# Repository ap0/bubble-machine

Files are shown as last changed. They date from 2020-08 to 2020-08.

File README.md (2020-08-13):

# Bubble Machine

This is the design and code for my bubble machine.  You can find more info at the blog post here: https://medium.com/@adamargo/an-arduino-powered-3d-printed-bubble-machine-4cf9241d1459

## Notes

The parts were designed from scratch in Fusion 360.  The electronics were designed to use a 5V input supply so they could be powered by phone batteries.  At max settings, my power supply reported that it was consuming about 1.4A, so I'd be safe and round up to 2A for the output on the USB port.

The Arduino code runs the stepper motion in the event loop so minimize jitters when updating the LCD.  The I2C LCD is very slow to update.  A better version might figure out how to output directly without I2C.

## Parts List

To build this, you will need:

* at least 4 feet of 3/8" dowel rods ($1 at Home Depot)
* 4x M3x10mm screws and square nuts (I bought these nuts: https://www.amazon.com/Honbay-100pcs-Stainless-Steel-Square/dp/B06XPFLNBS -- they are a little thicker than the nuts that come on e.g. the Prusa).  These can be longer than 10mm if you don't have any; that's just the minimum.
* 4x M2.5x12mm M2 screws and nuts for the LCD -- these can be a little longer if you don't have 12mm -- up to 15mm should be fine, they'll just stick out inside the housing.
* Type 130 12V motor (I used the ones from this kit https://www.amazon.com/EUDAX-Electric-Magnetic-Connector-Propeller/dp/B07GDP2FCL -- the red housing seems to be the key, because they're a standard type 130 size motor, but lower voltage ones do not work and will burn up)
* Arduino Nano
  * I got one with pins soldered onto the board. This makes it easy to slot into the protoboard.
* 2 10k+Ω potentiometers (ones with a 7mm shaft diameter)
* A 16x2 I2C LCD module (I got these: https://www.amazon.com/GeeekPi-Character-Backlight-Raspberry-Electrical/dp/B07S7PJYM6) -- this part isn't required for the machine to function -- you could easily redesign the housing to not use it.
* 50x75mm protoboard
* 2x 2-pin terminal blocks
* ULN2003A Darlington array and socket
* IRF520 or RFP30N06LE MOSFET (it has to be a logic-level MOSFET, i.e. can be driven by 5V from Arduino)
* 2.54mm header pins and sockets
* 4 .1 μF capacitors
* 2 diodes
* A 5V 2.0A power supply (1.4A is the highest output I've seen on the meter -- the fan motor draws a lot of energy at high speeds) -- if you limited the MOSFET's output then you could probably live with 1A.  I'm using an Anker battery pack and it works fine.

## 3D printed parts

Total print time is around 24 hours at .15mm quality settings in PrusaSlicer for a MK3S.  You can't quite fit everything onto the bed at once.  The parts are designed to have a face to print on and should require minimal supports.  You will have to block the gap on the outer ring of the fan mount.

### Supports you should add

I tried to make it use minimal supports.  You should only need them on three of the parts:
* On the blower fan motor holder, you should add a support under the small area that's a clearance for the cover to sit flush, and potentially to hold up the other side of the neck.  I added a small slab in PrusaSlicer and it worked fine.
* On the two knobs you'll have to add supports to the bottom because it's got some inset holes to sit flush over the potentiometer nuts.

I printed mine in a few different filaments.  I used orange Prusament PETG, the gray Prusa (not Prusament) PLA that came with the MK3s, and yellow and blue Hatchbox PLA.  No real rhyme or reason to it other than aesthetics.  PLA works well for the housing as it's quite large.  The housing uses about 100g of filament and took about 11 hours to print.  I really like Hatchbox PLA -- the colors are very nice, it's not very expensive, and it prints great.  I also printed the knobs in the same color of the part they control, just as a nice touch.

The bubble wand hub is the most challenging part to print.  I found that using 0.2mm layer heights worked slightly better to deposit a little more filament on the first layer to get the ridges to stick.  My final print of it had only two of those instances not stick.  The quality and calibration of your printer will make or break this part.

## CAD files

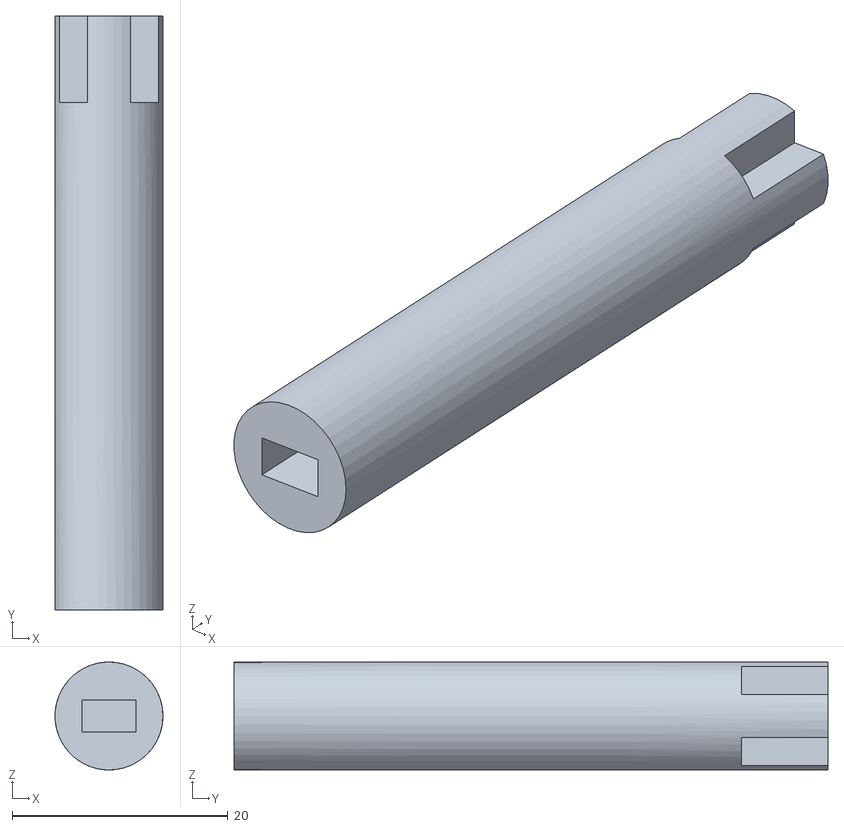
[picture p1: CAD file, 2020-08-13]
stl/BubbleMachine v25_BubbleMachine v25_Spindle_2_Spindle_Spindle.stl
10.0 x 55.0 x 9.99

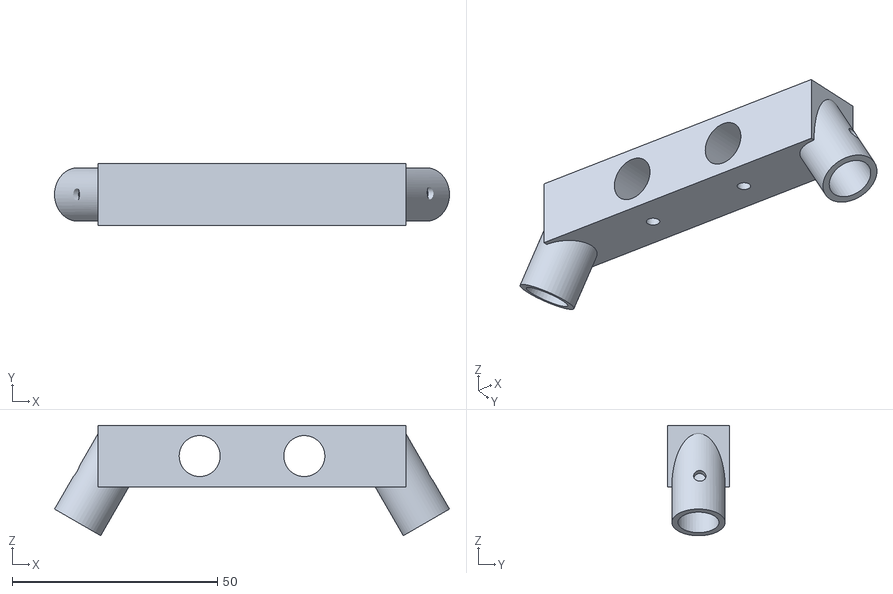
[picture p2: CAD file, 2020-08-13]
stl/BubbleMachine v25_BubbleMachine v25_Leg Mount _1_Leg Mount_.stl
96.3 x 15.0 x 26.9

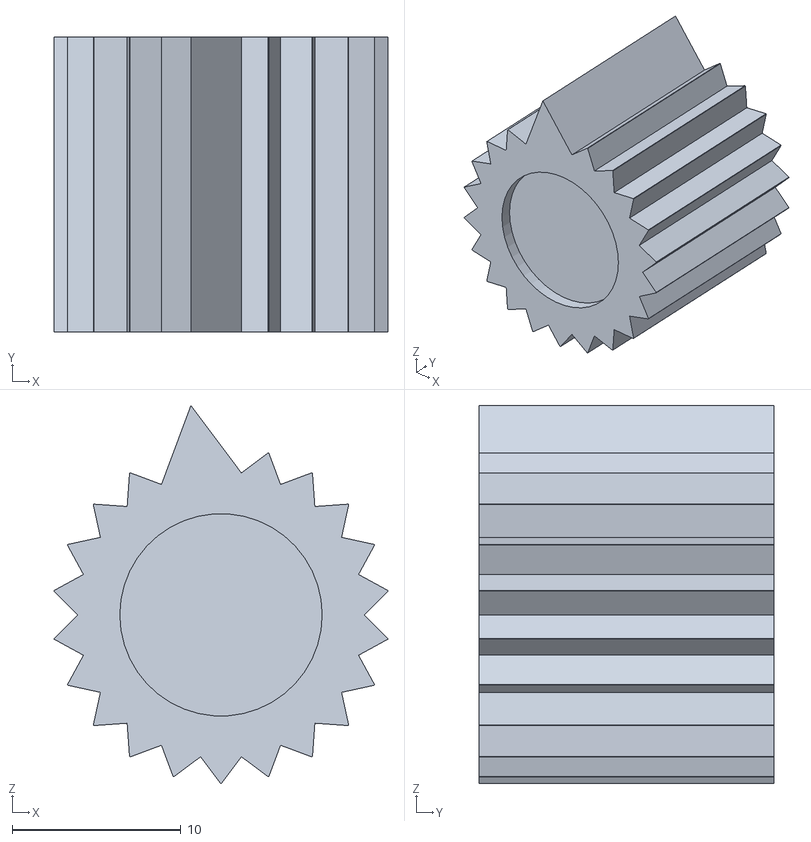
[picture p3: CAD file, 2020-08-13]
stl/BubbleMachine v25_BubbleMachine v25_Electronics Housing_1_KnurledKnob_1_Knob_KnurledKnob.stl
19.8 x 17.5 x 22.4

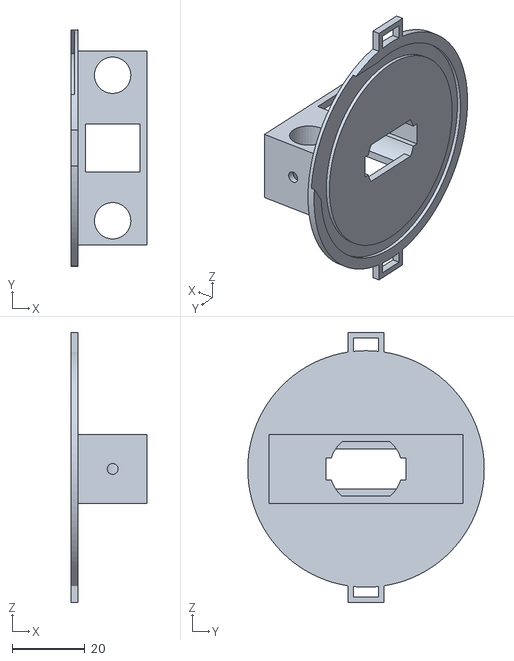
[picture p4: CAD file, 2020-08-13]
stl/BubbleMachine v25_BubbleMachine v25_Blower_1_Motor Holder_1_Holder_Motor Holder.stl
21.0 x 65.0 x 74.2

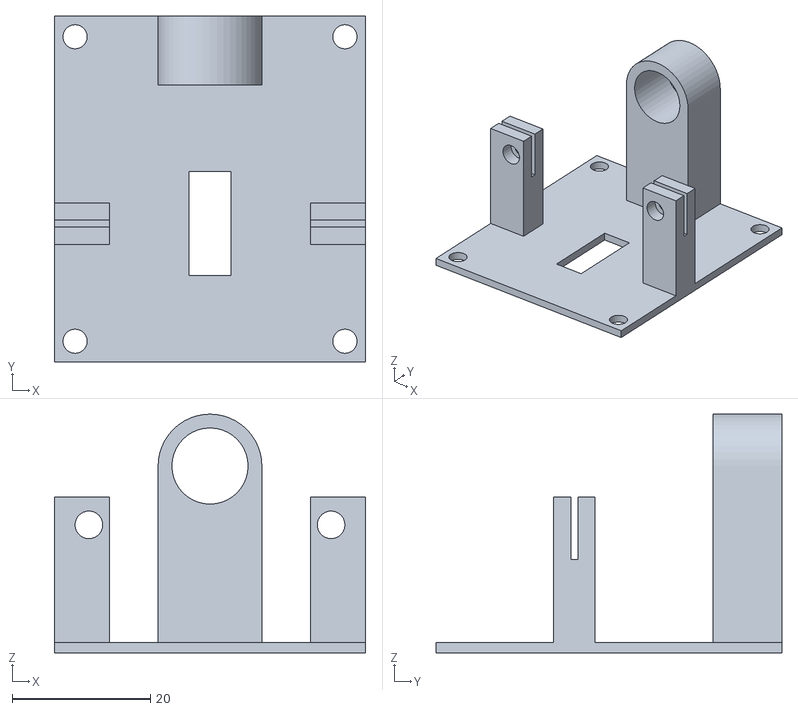
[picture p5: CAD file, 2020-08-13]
stl/BubbleMachine v25_BubbleMachine v25_Wand Motor Base_2_Base_Wand Motor Base.stl
45.0 x 50.0 x 34.5

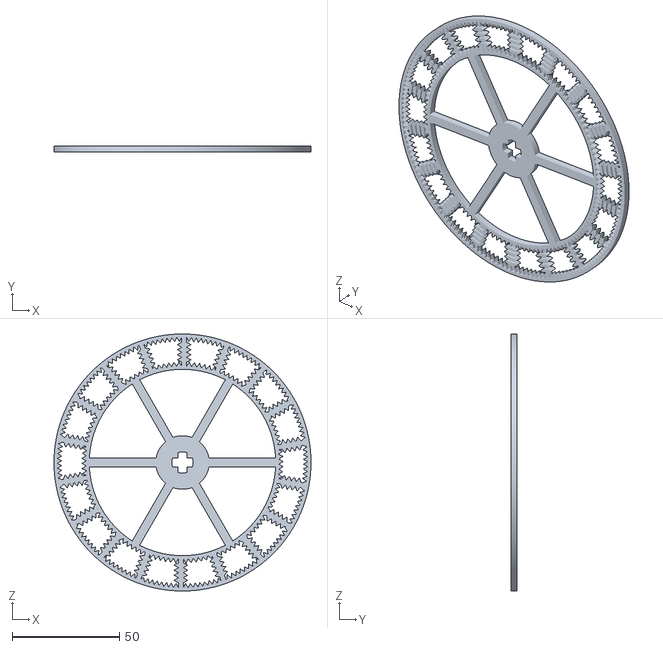
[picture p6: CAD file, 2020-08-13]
stl/BubbleMachine v25_BubbleMachine v25_Wand Wheel_1_Wheel_Wand Wheel.stl
120.0 x 3.00 x 120.0

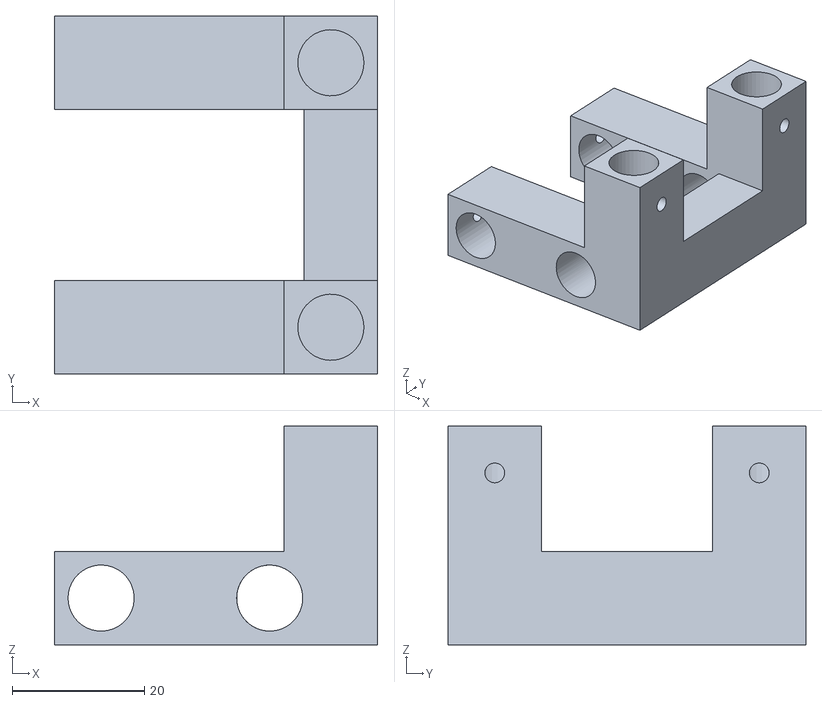
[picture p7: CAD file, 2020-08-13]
stl/BubbleMachine v25_BubbleMachine v25_Blower Frame Mount_1_Blower Frame Mount_.stl
48.9 x 54.1 x 33.1

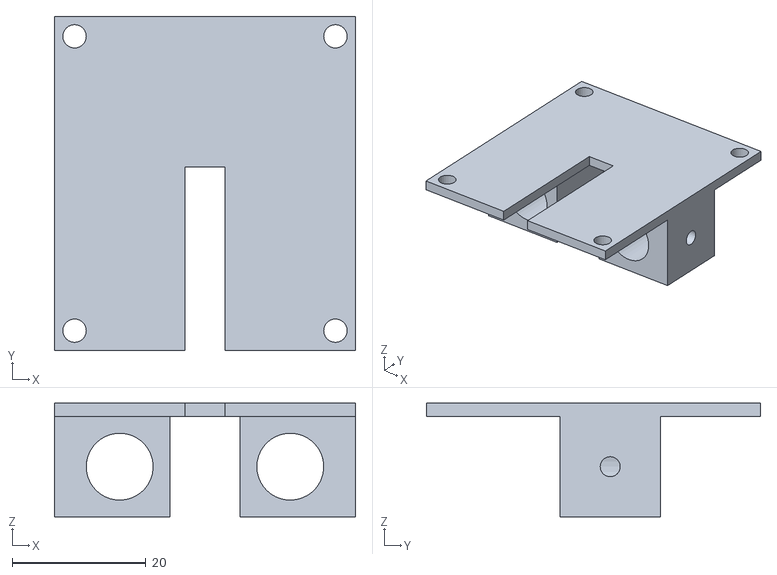
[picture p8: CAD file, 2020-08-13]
stl/BubbleMachine v25_BubbleMachine v25_Wand Motor Stand Base_1_Motor Stand Base_.stl
45.0 x 50.0 x 17.0

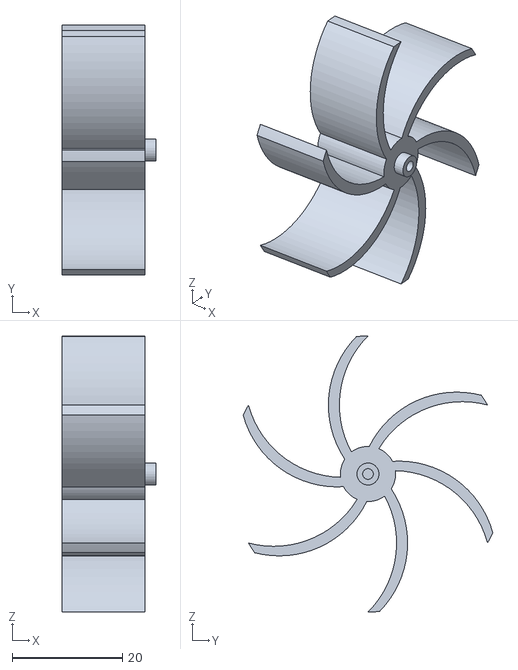
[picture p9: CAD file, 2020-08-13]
stl/BubbleMachine v25_BubbleMachine v25_Blower_1_Impeller_1_Impeller_Impeller.stl
17.0 x 45.2 x 50.0

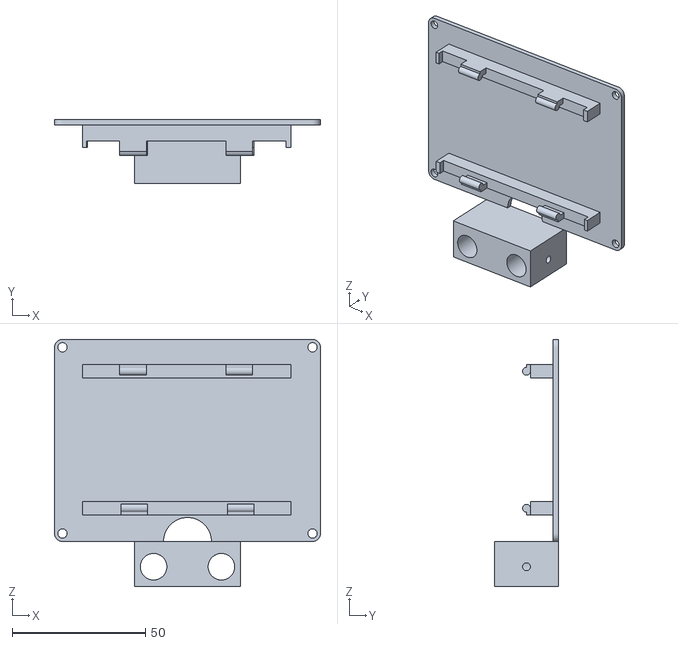
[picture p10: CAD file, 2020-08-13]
stl/BubbleMachine v25_BubbleMachine v25_Electronics Housing_1_Housing_1_Back_1_Back_Back.stl
100.0 x 24.0 x 93.0

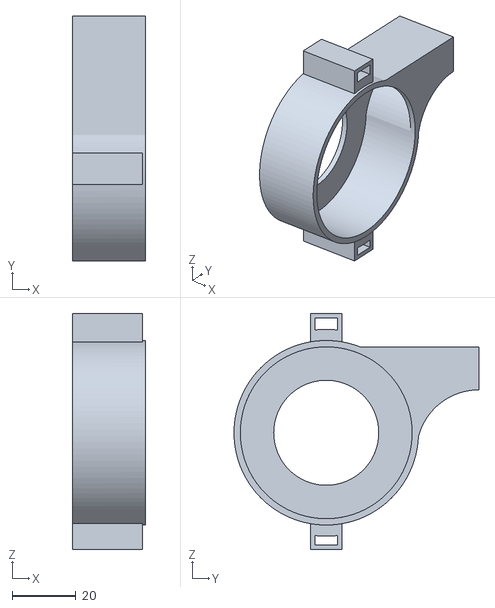
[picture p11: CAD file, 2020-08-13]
stl/BubbleMachine v25_BubbleMachine v25_Blower_1_Blower Cover_1_Cover_Blower Cover.stl
23.0 x 77.0 x 74.2

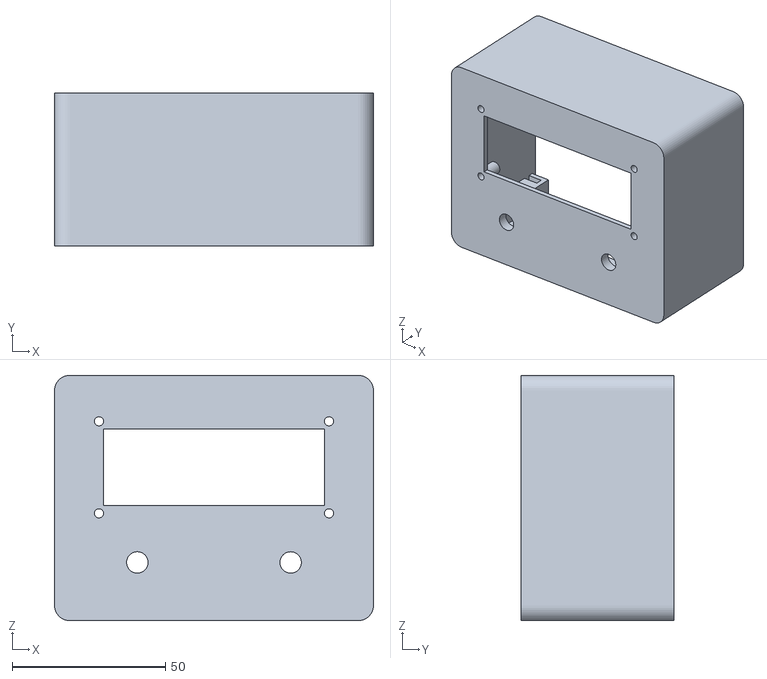
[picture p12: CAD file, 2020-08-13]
stl/BubbleMachine v25_BubbleMachine v25_Electronics Housing_1_Housing_1_Front Panel_1_Front Panel_Front Panel.stl
104.0 x 50.0 x 80.0

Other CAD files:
stl/BubbleMachine v25_BubbleMachine v25_Electronics Housing_1_KnurledKnob_2_Knob_KnurledKnob_1.stl
stl/BubbleMachine v25_BubbleMachine v25_Electronics Housing_1_KnurledKnob_1_Knob_KnurledKnob_1.stl

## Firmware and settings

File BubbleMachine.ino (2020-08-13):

#include <Wire.h>
#include <LiquidCrystal_I2C.h>

const int STEPS_PER_REVOLUTION = 2038;

const int WAND_POT_PIN = 1; //A1;
const int FAN_POT_PIN = 0;  //A0;

const int FAN_MOSFET_PIN = 3;

const int MAX_WAND_SPEED = 13;
const int MAX_FAN_SPEED = 21;

const int BUFFER_SIZE = 8;
const int REFRESH_INTERVAL = 500; //ms

const int LCD_WIDTH = 16;
const int LCD_HEIGHT = 2;

// We use rolling buffers of fixed size to track the last N values of a pin
// and then average them out to determine whether or not to change the value.
int wandVals[BUFFER_SIZE];
int fanVals[BUFFER_SIZE];
int wandPos = 0;
int fanPos = 0;

// Track fan speeds to make sure we're not updating unnecessarily
int lastWandSpeed = -1;
int lastFanSpeed = -1;

bool screenDirty = false;

const char *intro[] = {
    "oO0* Nora's *oO0",
    "*Oo Bubbles! oO*",
};
char lcdBuffer[17];

unsigned long lastUpdate = 0;
unsigned long lastStepMicros = 0;

/*
Note that I have modified how the stepper control works.  I'm not using the library but instead
ripped out the 4-pin version of it and have it process in the main event loop.

If you don't do this, you will have issues where the LCD and motor block each other and the whole system
appears very jittery.  This makes everything much smoother.
*/

// ** This is not the same wiring as you find on most examples!  This is so the circuit board wiring is simpler (see the schematic) **
// These values are just mapped from the standard 8, 10, 9, 11 configuration.
const int STEP_PIN_1 = 11;
const int STEP_PIN_2 = 9;
const int STEP_PIN_3 = 10;
const int STEP_PIN_4 = 8;

unsigned long stepDelay = 0;
int curStep = 0;

// Convert RPM to microseconds per step for use in the event loop.
void setStepperRPM(long rpm)
{
    if (rpm == 0)
    {
        stepDelay = 0;
        return;
    }
    stepDelay = 60L * 1000L * 1000L / STEPS_PER_REVOLUTION / rpm;
}

// Copied straight from Stepper.h
void stepMotor(int stepNum)
{
    switch (stepNum)
    {
    case 0: // 1010
        digitalWrite(STEP_PIN_1, HIGH);
        digitalWrite(STEP_PIN_2, LOW);
        digitalWrite(STEP_PIN_3, HIGH);
        digitalWrite(STEP_PIN_4, LOW);
        break;
    case 1: // 0110
        digitalWrite(STEP_PIN_1, LOW);
        digitalWrite(STEP_PIN_2, HIGH);
        digitalWrite(STEP_PIN_3, HIGH);
        digitalWrite(STEP_PIN_4, LOW);
        break;
    case 2: //0101
        digitalWrite(STEP_PIN_1, LOW);
        digitalWrite(STEP_PIN_2, HIGH);
        digitalWrite(STEP_PIN_3, LOW);
        digitalWrite(STEP_PIN_4, HIGH);
        break;
    case 3: //1001
        digitalWrite(STEP_PIN_1, HIGH);
        digitalWrite(STEP_PIN_2, LOW);
        digitalWrite(STEP_PIN_3, LOW);
        digitalWrite(STEP_PIN_4, HIGH);
        break;
    }
}

LiquidCrystal_I2C lcd = LiquidCrystal_I2C(0x27, 2, 1, 0, 4, 5, 6, 7, 3, POSITIVE);

const char randChars[] = "o0O *";
char bufStr[LCD_WIDTH + 1];

// Prints random 'bubble' characters in the specified portions of the LCD
void randLcd(int start, int len, int line)
{
    for (int i = 0; i < len; i++)
    {
        bufStr[i] = randChars[random(5)];
    }
    bufStr[len] = '\0';

    lcd.setCursor(start, line);
    lcd.print(bufStr);
}

void setup()
{
    randomSeed(analogRead(2));
    pinMode(FAN_MOSFET_PIN, OUTPUT);
    pinMode(STEP_PIN_1, OUTPUT);
    pinMode(STEP_PIN_2, OUTPUT);
    pinMode(STEP_PIN_3, OUTPUT);
    pinMode(STEP_PIN_4, OUTPUT);

    initArray(wandVals, BUFFER_SIZE);
    initArray(fanVals, BUFFER_SIZE);

    Wire.begin();
    lcd.begin(LCD_WIDTH, LCD_HEIGHT);
    lcd.backlight();

    lcd.setCursor(0, 0);
    lcd.print(intro[0]);
    lcd.setCursor(0, 1);
    lcd.print(intro[1]);

    // Sample inputs before we get started
    int startTime = millis();

    while (millis() - startTime < 2000)
    {

        int wandVal = analogRead(WAND_POT_PIN);
        int fanVal = analogRead(FAN_POT_PIN);
        updateArray(wandVal, wandVals, &wandPos, BUFFER_SIZE);
        updateArray(fanVal, fanVals, &fanPos, BUFFER_SIZE);

        randLcd(0, 4, 0);
        randLcd(12, 4, 0);
        randLcd(0, 3, 1);
        randLcd(13, 3, 1);
        delay(150);
    }

    // Set up template values -- we will only refresh the number elements in the loop.
    lcd.setCursor(0, 0);

    //  lcd.print("Fan Speed:    %");
    lcd.print("oO0oOo Fan:    %");
    lcd.setCursor(0, 1);
    //  lcd.print("Wand Speed:    %");
    lcd.print("oO0Oo Wand:    %");
}

int average(int vals[], int arrSize)
{
    int sum = 0;
    for (int i = 0; i < arrSize; i++)
    {
        sum += vals[i];
    }

    return sum / arrSize;
}

int initArray(int vals[], int arrSize)
{
    for (int i = 0; i < arrSize; i++)
    {
        vals[i] = 0;
    }
}

// Adds a value to the buffer and returns the average value of it.
int updateArray(int val, int vals[], int *pos, int arrSize)
{
    // Only dereference once
    int thisPos = *pos;
    if (thisPos < 0 || thisPos >= arrSize)
        *pos = 0;

    vals[thisPos] = val;

    if (thisPos == arrSize - 1)
    {
        *pos = 0;
    }
    else
    {
        *pos = thisPos + 1;
    }

    return average(vals, arrSize);
}

bool firstLineUpdate = false;
int firstLineCursor = 0;
int secondLineCursor = 0;
void loop()
{

    int wandVal = updateArray(analogRead(WAND_POT_PIN), wandVals, &wandPos, BUFFER_SIZE);
    int fanVal = updateArray(analogRead(FAN_POT_PIN), fanVals, &fanPos, BUFFER_SIZE);

    // Use unsigned ints so they can never go below 0.  I saw the value be -8 once and was baffled.
    unsigned long wandSpeed = map(wandVal, 0, 1023, 0, MAX_WAND_SPEED);
    unsigned long fanSpeed = map(fanVal, 0, 1023, 0, MAX_FAN_SPEED);

    // HACK
    // Do -1 because it sometimes flops at the last increment between MAX and MAX-1
    // Here we just make the actual max MAX-1.
    wandSpeed = (wandSpeed >= MAX_WAND_SPEED ? MAX_WAND_SPEED - 1 : wandSpeed);
    if (wandSpeed != lastWandSpeed)
    {
        // wandStepper.setSpeed(wandSpeed);
        setStepperRPM(wandSpeed);

        lastWandSpeed = wandSpeed;

        screenDirty = true;
    }

    // Use the current time of the loop to determine when to move to the next step.
    // This smooths out the motion while also letting the LCD update.
    // It might not be perfectly tight from a precision perspective but it's close enough.

    fanSpeed = (fanSpeed >= MAX_FAN_SPEED ? MAX_FAN_SPEED - 1 : fanSpeed);
    if (fanSpeed != lastFanSpeed)
    {
        // Don't go full 255 here.
        // Motor already draws enough current as it is.
        analogWrite(FAN_MOSFET_PIN, map(fanSpeed, 0, MAX_FAN_SPEED, 0, 245));

        lastFanSpeed = fanSpeed;

        screenDirty = true;
    }

    // Loop until we can step the motor.
    // After we step it, update the screen if necessary.
    while (true)
    {
        unsigned long now = micros();
        // We want to make sure we don't get into an infinite loop if the stepper isn't moving.

        if (now - lastStepMicros >= stepDelay || stepDelay == 0)
        {
            if (stepDelay > 0)
            {
                stepMotor(curStep % 4);
                curStep++;
                if (curStep == 4)
                {
                    curStep = 0;
                }
            }
            lastStepMicros = now;

            // Only do screen updates immediately after stepping the motor.
            if (screenDirty)
            {
                // Only update the values we need to
                sprintf(lcdBuffer, "%3d", map(fanSpeed, 0, MAX_FAN_SPEED - 1, 0, 100));
                lcd.setCursor(12, 0);
                lcd.print(lcdBuffer);

                sprintf(lcdBuffer, "%3d", map(wandSpeed, 0, MAX_WAND_SPEED - 1, 0, 100));
                lcd.setCursor(12, 1);
                lcd.print(lcdBuffer);

                screenDirty = false;
            }

            if (now - lastUpdate > REFRESH_INTERVAL * 1000L)
            {
                if (firstLineUpdate)
                {
                    randLcd(0, 6, 0);
                }
                else
                {
                    randLcd(0, 5, 1);
                }
                firstLineUpdate = !firstLineUpdate;
                lastUpdate = now;
            }
            return;
        }
    }
}
